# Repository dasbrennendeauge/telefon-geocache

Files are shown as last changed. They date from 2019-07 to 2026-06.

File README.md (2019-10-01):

## telefon-geocache

### Idee

Hörer abheben 
-> Ist die aktuelle Uhrzeit zwischen 8 und 22 Uhr? (RTC)
--> Nein? --> Displayanzeige "Dieses Gerät ist nur zwischen 8 und 22 Uhr verfügbar."

-> Arduino start -> GSM start
-> Displayanzeige "Hallo"
-> Sound abspielen "Hallo, willkommen zu meinem Cache. Du hast 5 Minuten Zeit und nur einen Versuch."
-> Display zeigt 5-Minuten-Zähler an

-> Displayanzeige & Sound: "Gib deine Handynummer ein und drücke die Rautetaste."

-> Zahleneingabe
-> Raute gedrückt?

-> Displayanzeige "Münze einwerfen"
-> Sound abspielen "Wirf eine Münze ein, damit das Spiel gestartet wird."

-> Münze eingeworfen? (Lichtschranke)
-> Displayanzeige & Sound: "Danke"

-> GSM bereit?
-> Verbindungsaufbau mit spezieller Rufnummer (z.B. 0211-1234-1337)
-> Klingeln?
-> Auflegen.

-> Displayanzeige & Sound: "Gib die letzten 4 Stellen des Anrufers ein."
-> Richtig?
-> Klappe unten öffnet (Relais)
-> Displayanzeige & Sound: "Trag dich ein, schließ die Klappe und häng auf."

### bisherige Umsetzung

(http://www.youtube.com/watch?v=i5rzEiwlTfw "")

### Benötigte Elektronik:
- Arduino Mega
- MP3-Player DFPlayerMini (2)
- Display	(2)
- Step Up Modul
- GSM-Modul	SIM800L (3)
- Keypad	(7)
- Lichtschranke (1)
- Relais SRD-05VDC-SL-C	(1)
- (Lautsprecher)

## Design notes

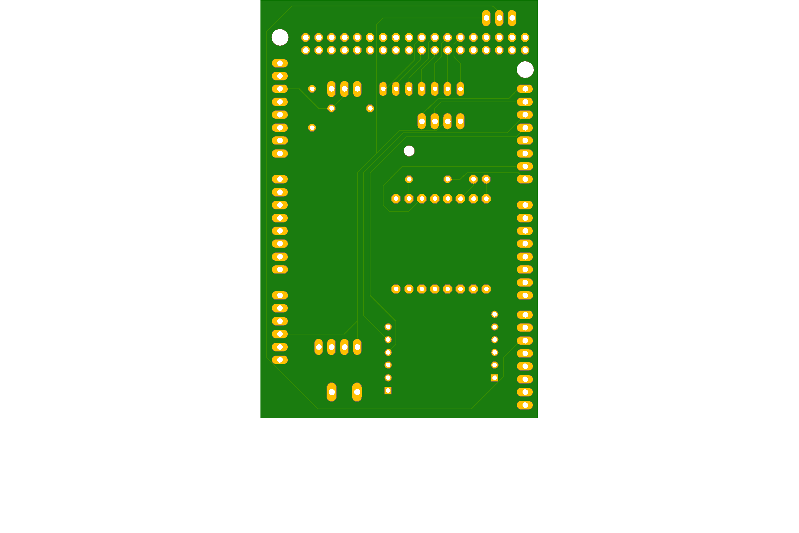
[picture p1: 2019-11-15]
pcb/cache/cache2-bottom.png

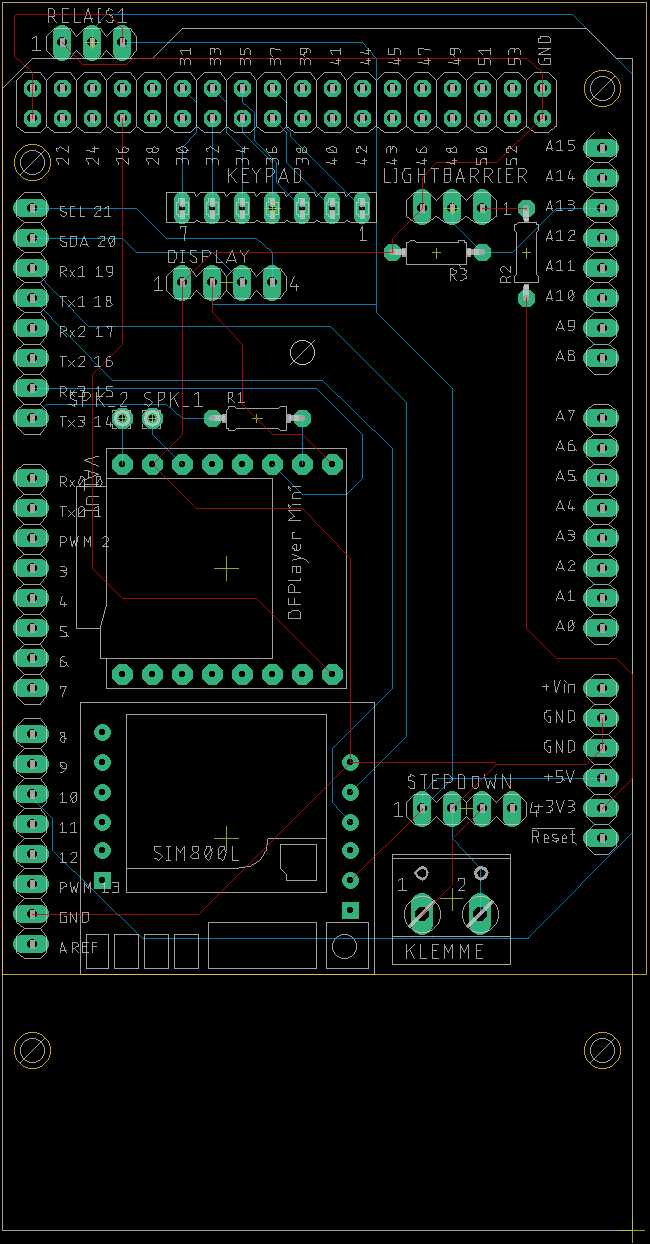
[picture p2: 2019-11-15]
pcb/cache/cache2-board.png

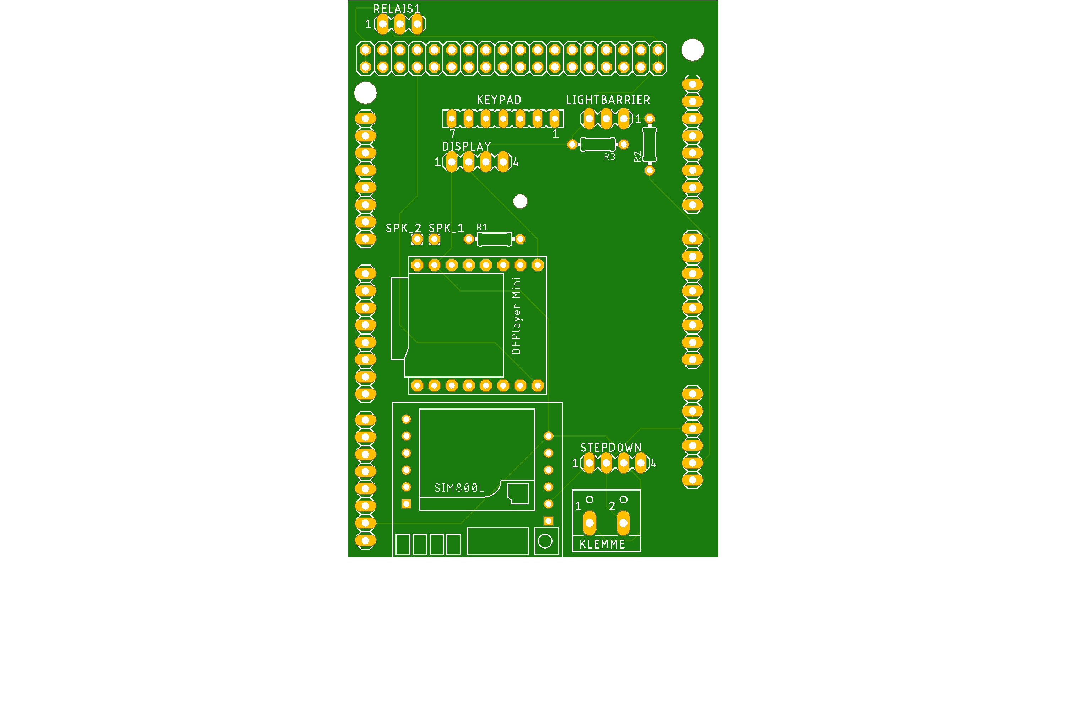
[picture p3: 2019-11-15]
pcb/cache/cache2-top.png

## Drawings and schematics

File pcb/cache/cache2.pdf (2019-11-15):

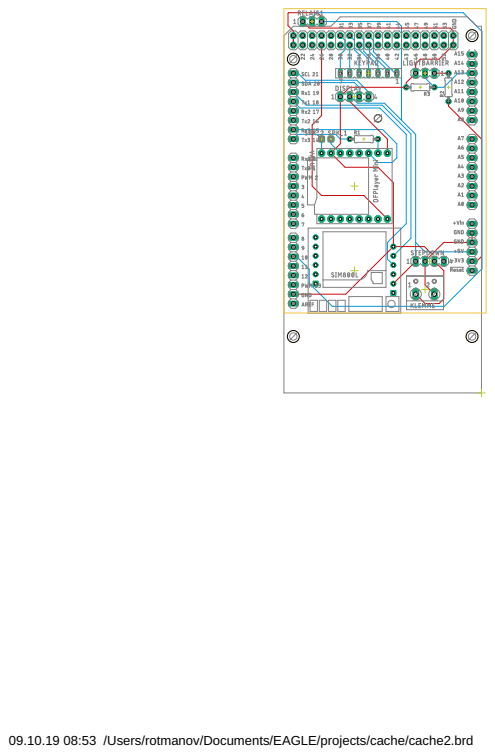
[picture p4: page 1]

09.10.19 08:53 /Users/rotmanov/Documents/EAGLE/projects/cache/cache2.brd

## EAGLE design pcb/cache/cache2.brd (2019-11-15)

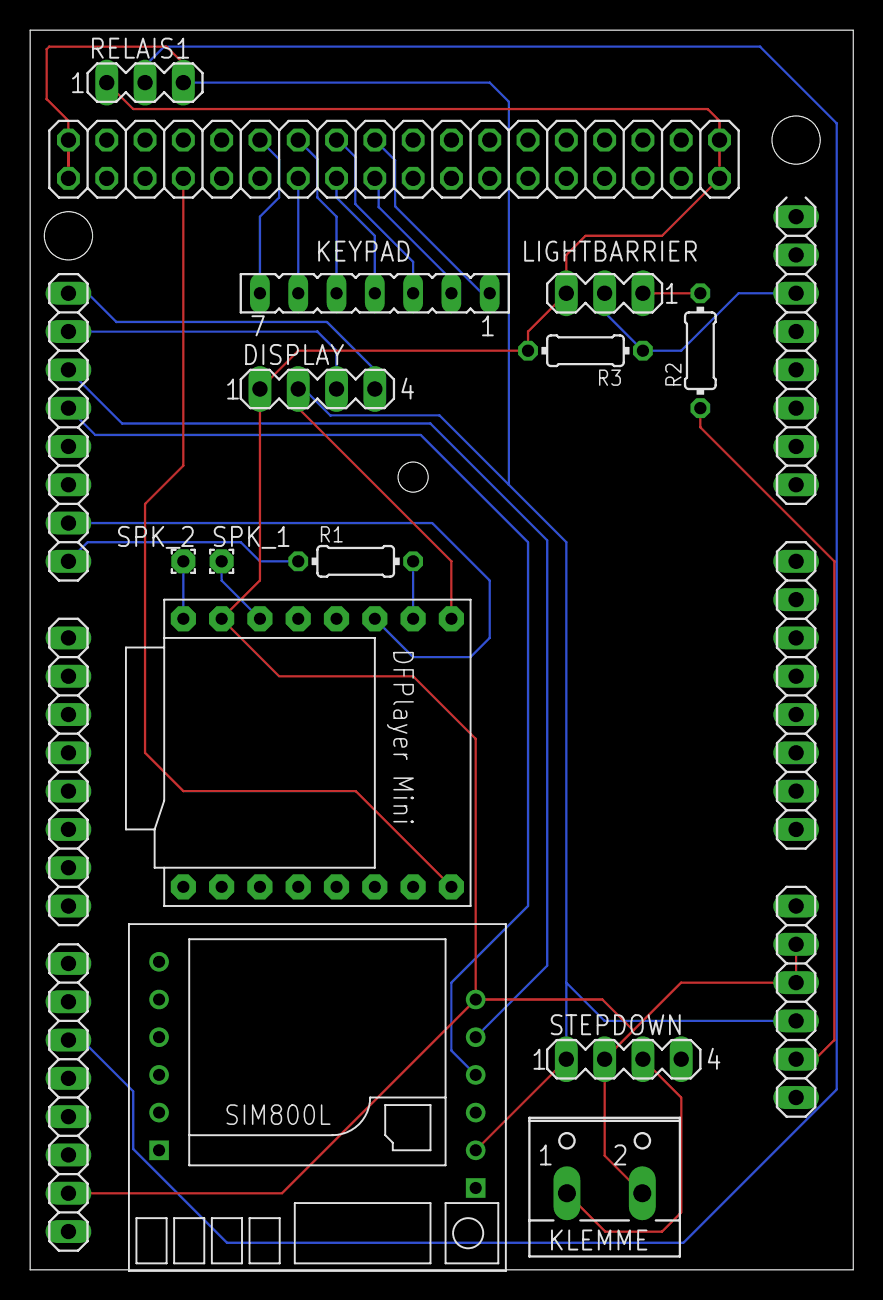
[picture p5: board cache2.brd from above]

Board: 2 copper layers, 54.6 x 82.2 mm, 14 parts (0 on the bottom side), 24 nets.

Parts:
DISPLAY: MA04-1
IC1: MEGA_ARDUINO
KEYPAD: FE07
KLEMME: W237-102
LIGHTBARRIER: MA03-1
R1, R2, R3: 0204/7
RELAIS1: MA03-1
SPK_1, SPK_2: 1,6/0,8
STEPDOWN: MA04-1
U$1: DFPLAYER
U$2: SIM800LMODULE

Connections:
3V3: LIGHTBARRIER.1, R2.2
+5V: DISPLAY.2, IC1.3, IC1.47, IC1.48, RELAIS1.3, STEPDOWN.1, U$1.VCC, U$2.VCC
GND: DISPLAY.1, IC1.4, IC1.5, IC1.45, IC1.81, IC1.82, KLEMME.2, LIGHTBARRIER.3, R3.2, RELAIS1.1, STEPDOWN.2, U$1.GND_1, U$2.GND
IN+: KLEMME.1, STEPDOWN.3
IN-B: IC1.20, LIGHTBARRIER.2, R3.1
unnamed: IC1.25, U$2.TX
unnamed: IC1.26, U$2.RX
unnamed: IC1.41, RELAIS1.2
unnamed: DISPLAY.3, IC1.24
unnamed: DISPLAY.4, IC1.23
unnamed: IC1.58, KEYPAD.7
unnamed: IC1.59, KEYPAD.6
unnamed: IC1.60, KEYPAD.5
unnamed: IC1.61, KEYPAD.4
unnamed: IC1.62, KEYPAD.3
unnamed: IC1.63, KEYPAD.2
unnamed: IC1.64, KEYPAD.1
unnamed: IC1.30, R1.1
unnamed: IC1.29, U$1.TX
unnamed: R1.2, U$1.RX
unnamed: IC1.2, R2.1
unnamed: SPK_2.1, U$1.SPK2
unnamed: SPK_1.1, U$1.SPK1
unnamed: IC1.53, U$1.BUSY

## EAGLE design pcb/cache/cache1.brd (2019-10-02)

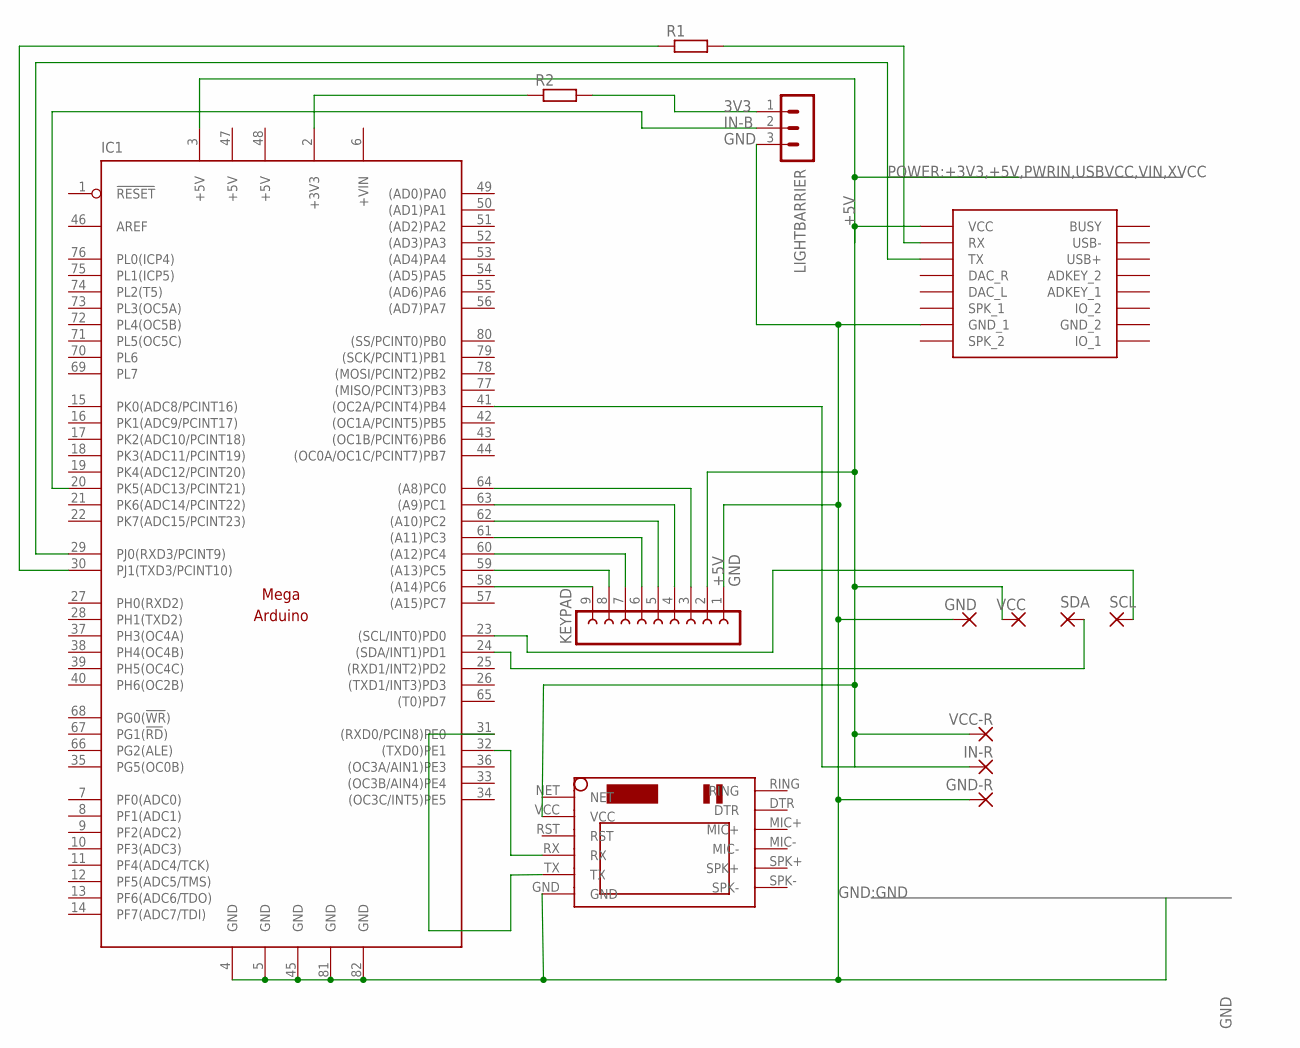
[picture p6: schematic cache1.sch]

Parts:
GND: 1,6/0,8
GND-R: 1,6/0,8
IC1: MEGAARDUINO_1; MEGA_ARDUINO
IN-R: 1,6/0,8
KEYPAD: FE09-1; FE09
LIGHTBARRIER: MA03-1
R1, R2: R-EU_0204/7; 0204/7
SCL: 1,6/0,8
SDA: 1,6/0,8
U$1: DFPLAYER
U$2: SIM800LMODULE
VCC: 1,6/0,8
VCC-R: 1,6/0,8

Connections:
3V3: LIGHTBARRIER.1, R2.2
+5V: IC1.3 (+5V), IC1.47 (+5V), IC1.48 (+5V), KEYPAD.2, U$1.VCC, U$2.VCC, VCC.1, VCC-R.1
+VIN: IC1.6 (+VIN)
GND: GND.1, GND-R.1, IC1.4 (GND), IC1.5 (GND), IC1.45 (GND), IC1.81 (GND), IC1.82 (GND), KEYPAD.1, LIGHTBARRIER.3, U$1.GND_1, U$2.GND
IN-B: IC1.20 (PK5(ADC13/PCINT21)), LIGHTBARRIER.2
unnamed: IC1.31 ((RXD0/PCIN8)PE0), U$2.TX
unnamed: IC1.32 ((TXD0)PE1), U$2.RX
unnamed: IC1.41 ((OC2A/PCINT4)PB4), IN-R.1
unnamed: IC1.24 ((SDA/INT1)PD1), SDA.1
unnamed: IC1.23 ((SCL/INT0)PD0), SCL.1
unnamed: IC1.58 ((A14)PC6), KEYPAD.9
unnamed: IC1.59 ((A13)PC5), KEYPAD.8
unnamed: IC1.60 ((A12)PC4), KEYPAD.7
unnamed: IC1.61 ((A11)PC3), KEYPAD.6
unnamed: IC1.62 ((A10)PC2), KEYPAD.5
unnamed: IC1.63 ((A9)PC1), KEYPAD.4
unnamed: IC1.64 ((A8)PC0), KEYPAD.3
unnamed: IC1.30 (PJ1(TXD3/PCINT10)), R1.1
unnamed: IC1.29 (PJ0(RXD3/PCINT9)), U$1.TX
unnamed: R1.2, U$1.RX
unnamed: IC1.2 (+3V3), R2.1

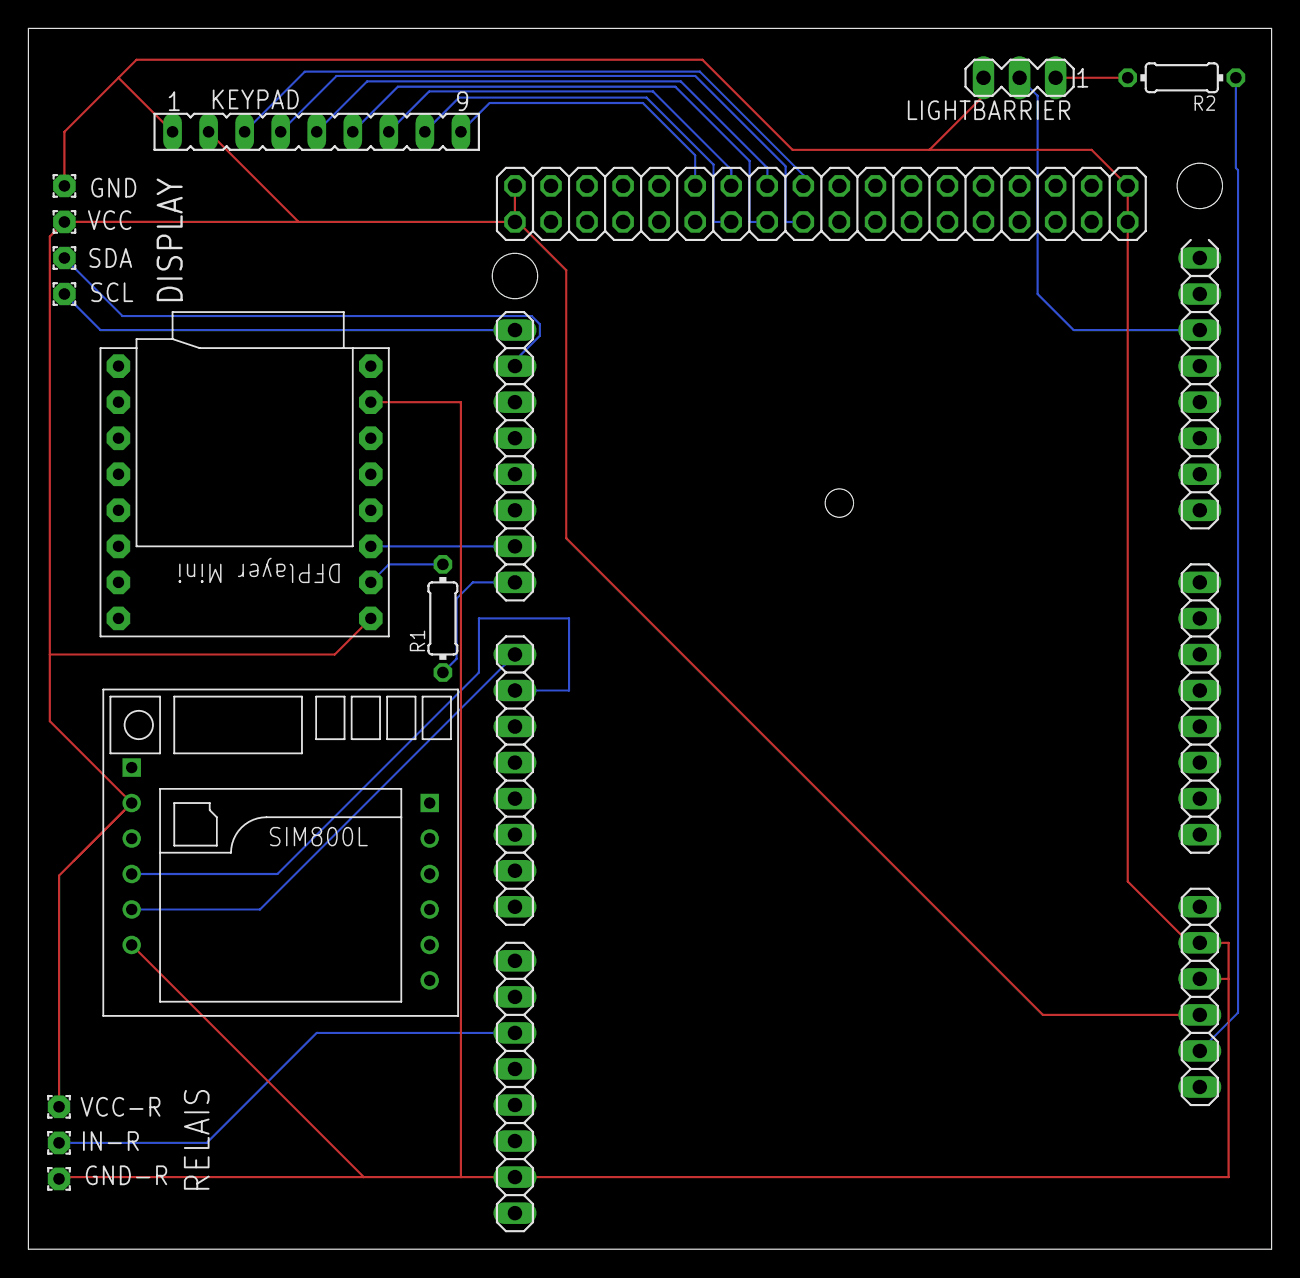
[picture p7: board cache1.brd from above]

Board: 2 copper layers, 87.6 x 86.0 mm, 14 parts (0 on the bottom side), 20 nets.

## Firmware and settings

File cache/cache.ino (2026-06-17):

#include <avr/sleep.h>
#include <LiquidCrystal_I2C.h>
#include <DFMiniMp3.h>
#include <SoftwareSerial.h>
#include <Keypad.h>

// GSM Calls: https://www.activexperts.com/serial-port-component/tutorials/gsmdial/

#define TIME_TO_LIVE 300
#define RELAIS_PIN 10
#define TINY_GSM_DEBUG Serial

const byte ROWS = 4; // Four rows
const byte COLS = 3; // Three columns
// Define the Keymap
char keys[ROWS][COLS] = {
  {'1', '2', '3'},
  {'4', '5', '6'},
  {'7', '8', '9'},
  {'#', '0', '*'}
};
// Connect keypad ROW0, ROW1, ROW2 and ROW3 to these Arduino pins.
byte rowPins[ROWS] = { 34, 35, 36, 37 };
// Connect keypad COL0, COL1 and COL2 to these Arduino pins.
byte colPins[COLS] = { 31, 32, 33 };
// Create the Keypad
Keypad kpd = Keypad( makeKeymap(keys), rowPins, colPins, ROWS, COLS );

const int analogInPin = A13;  // Data Muenzeinwurf

// set GSM PIN, if any
#define GSM_PIN "6348"

// DFPlayer Mini
SoftwareSerial mySoftwareSerial(2, 3); // RX, TX
// implement a notification class,
// its member methods will get called
//
class Mp3Notify {
  public:
    static void OnError(uint16_t errorCode) {
      // see DfMp3_Error for code meaning
      Serial.println();
      Serial.print("Com Error ");
      Serial.println(errorCode);
    }
    static void OnPlayFinished(uint16_t track) {
      Serial.print("Track beendet ");
      Serial.println(track);
      delay(100);
      // TODO: nächsten Schritt aufrufen
    }
    static void OnCardOnline(uint16_t code) {
      Serial.println(F("SD Karte online "));
    }
    static void OnCardInserted(uint16_t code) {
      Serial.println(F("SD Karte bereit "));
    }
    static void OnCardRemoved(uint16_t code) {
      Serial.println(F("SD Karte entfernt "));
    }
    static void OnUsbOnline(uint16_t code) {
      Serial.println(F("USB online "));
    }
    static void OnUsbInserted(uint16_t code) {
      Serial.println(F("USB bereit "));
    }
    static void OnUsbRemoved(uint16_t code) {
      Serial.println(F("USB entfernt "));
    }
};
static DFMiniMp3<HardwareSerial, Mp3Notify> mp3(Serial3);

LiquidCrystal_I2C lcd(0x27, 20, 4); //Hier wird das Display benannt. In unserem //Fall „lcd“. Die I²C Adresse (Erläuterung und I²C Adressen Scanner in folgender Anleitung: Link zur Anleitung „2 I²C Displays gleichzeitig“) 0x27 wird auch angegeben.

// Select your modem:
#define TINY_GSM_MODEM_SIM800

// Increase RX buffer to capture the entire response
// Chips without internal buffering (A6/A7, ESP8266, M590)
// need enough space in the buffer for the entire response
// else data will be lost (and the http library will fail).
#define TINY_GSM_RX_BUFFER 512

// Set serial for AT commands (to the module)
// Use Hardware Serial on Mega
// RX118 & TX119
#define SerialAT Serial1

// Your GPRS credentials
// Leave empty, if missing user or pass
const char apn[]  = "sipgate";
const char gprsUser[] = "sipgate";
const char gprsPass[] = "sipgate";

// Server details
const char server[] = "dev.rotmanov.de";
String url = String("/?number=");
const int port = 9992;

#include <TinyGsmClient.h>
#include <ArduinoHttpClient.h>

TinyGsm modem(SerialAT);
TinyGsmClient client(modem);
HttpClient http(client, server, port);

unsigned long startMillis;
unsigned long stepStartMillis;
int step = 0;
bool refreshDisplay = false;
bool outOfOrder = false;

String phoneNumber = String("");

String expected = String("4711"); // TODO: ersetze mit angerufener Nummer
String pin = String("");

void setup() {
  Serial.begin(115200); // Es gibt ein paar Debug Ausgaben über die serielle Schnittstelle
  Serial.println("Arduino start");

  pinMode(RELAIS_PIN, OUTPUT);
  digitalWrite(RELAIS_PIN, HIGH); //An dieser Stelle würde das Relais einsschalten

  // DFPlayer Mini initialisieren
  mp3.begin();
  mp3.setVolume(15);

  // -> Arduino start -> GSM start
  lcd.begin();
  lcd.backlight();//Beleuchtung des Displays einschalten
  startMillis = millis();
  refreshDisplay = true;
}

// -> Displayanzeige "Hallo, willkommen zu meinem Cache. Du hast 5 Minuten Zeit und nur einen Versuch."
// -> Sound abspielen "Hallo, willkommen zu meinem Cache. Du hast 5 Minuten Zeit und nur einen Versuch."
// -> Display zeigt 5-Minuten-Zähler an

void loop() {
  mp3.loop();
  if (step == 0) {
    step0();
  } else if (step == 1) {
    step1();
  } else if (step == 2) {
    step2();
  } else if (step == 3) {
    step3();
  } else if (step == 4) {
    step4();
  } else if (step == 5) {
    step5();
  } else if (step == 6) {
    step6();
  } else if (step == 7) {
    step7();
  }
  decreaseTimer();
}

void step0() {
  if (refreshDisplay == true) {
    showText(
      "H\xEFrer ans Ohr!      ",
      "                    ",
      "Dr""\xF5""cke dann Taste 5 ");
    refreshDisplay = false;

    // Set GSM module baud rate
    SerialAT.begin(19200);
    Serial.println("GSM start");

    // Restart takes quite some time
    // To skip it, call init() instead of restart()
    Serial.println("Initializing modem...");
    // modem.restart();
    modem.init();

    String modemInfo = modem.getModemInfo();
    Serial.print("Modem: ");
    Serial.println(modemInfo);

    if ( GSM_PIN && modem.getSimStatus() != 3 ) {
      modem.simUnlock(GSM_PIN);
    }
  }

  /*
  unsigned long currentMillis = millis();
  int secondsElapsed = (currentMillis - startMillis) / 1000;
  if (secondsElapsed > 2) {
  */
  char key = kpd.getKey();
  if (key) {
    step = 1;
    mp3.playMp3FolderTrack(1);
    stepStartMillis = millis();
    refreshDisplay = true;
  }
}

void step1() {
  if (refreshDisplay == true) {
    showText(
      "Willkommen!         ",
      "Deine Zeit l\xE1uft... ",
      "                    ");
    refreshDisplay = false;

  unsigned long startMillis = millis();
    Serial.println("Waiting for network...");

    modem.waitForNetwork();
    if (modem.isNetworkConnected()) {
      unsigned long currentMillis = millis();
      int secondsElapsed = (currentMillis - startMillis) / 1000;
      Serial.print("Network connected");
      Serial.println(secondsElapsed);
    }

    delay(500);
    
    String gsmTime = modem.getGSMDateTime(DATE_TIME);
    Serial.print("GSM Time:");
    Serial.println(gsmTime);
    String hour = gsmTime.substring(0, 2);
    Serial.println(hour);
    int hourI = hour.toInt();
    if(hourI > 21) {
      outOfOrder = true;
    }
    if(hourI < 8) {
      outOfOrder = true;
    }
    // String gsmDate = modem.getGSMDateTime(DATE_DATE);
    // Serial.print("GSM Date:");
    // Serial.println(gsmDate);
  }

  unsigned long currentMillis = millis();
  int secondsElapsed = (currentMillis - stepStartMillis) / 1000;
  if (secondsElapsed > 6) {
    if(outOfOrder) {
      stepStartMillis = millis();
      step = 7;
    } else {
      step = 2;      
      mp3.playMp3FolderTrack(2);
    }
    refreshDisplay = true;
  }
}

void step2() {
  if (refreshDisplay == true) {
    lcd.clear();
    showText(
      "Deine Handynummer:  ",
      phoneNumber.c_str(),
      "Ende mit Leertaste  ");
    refreshDisplay = false;
  }

  char key = kpd.getKey();
  if (key) {
    if (key == '#') {
      step = 3;
      url.concat(phoneNumber);
      mp3.playMp3FolderTrack(3);
      refreshDisplay = true;
      return;
    }
    phoneNumber.concat(key);
    refreshDisplay = true;
  }
}

void step3() {
  if (refreshDisplay == true) {
    showText(
      "M\xF5nze einwerfen     ",
      "                    ",
      "(Keine R""\xF5""ckgabe)    ");

    refreshDisplay = false;
  }

  // read the analog in value:
  int sensorValue = analogRead(analogInPin);

  if (sensorValue != 0) {
    step = 4;
    mp3.playMp3FolderTrack(4);
    stepStartMillis = millis();
    refreshDisplay = true;
    Serial.println("Pling!");
  }
}

void step4() {
  if (refreshDisplay == true) {
    showText(
      "Danke.              ",
      "Ich rufe dich an.   ",
      "NICHT ABHEBEN!      ");

    Serial.print("Waiting for network...");
    if (!modem.waitForNetwork()) {
      Serial.println(" fail");
      delay(10000);
      return;
    }
    Serial.println(" OK");

    if (modem.isNetworkConnected()) {
      Serial.println("Network connected");
    }

    Serial.print(F("Connecting to "));
    Serial.print(apn);
    if (!modem.gprsConnect(apn, gprsUser, gprsPass)) {
      Serial.println(" fail");
      delay(10000);
      return;
    }
    Serial.println(" OK");

    Serial.print(F("Performing HTTP GET request... "));
    Serial.print(url);
    int err = http.get(url);
    if (err != 0) {
      Serial.println(F("failed to connect"));
      delay(10000);
      return;
    }

    int status = http.responseStatusCode();
    Serial.print(F("Response status code: "));
    Serial.println(status);
    if (!status) {
      delay(10000);
      return;
    }

    String body = http.responseBody();
    Serial.println(F("Response:"));
    Serial.println(body);

    Serial.print(F("Body length is: "));
    Serial.println(body.length());

    expected = body;

    // Shutdown
    http.stop();
    Serial.println(F("Server disconnected"));

    modem.gprsDisconnect();
    Serial.println(F("GPRS disconnected"));

    step = 5;
    mp3.playMp3FolderTrack(5);
    refreshDisplay = true;
  }
}

void step5() {
  if (refreshDisplay == true) {
    lcd.clear();
    showText(
      "Wer rief dich an?   ",
      "Gib letzte 4 Zahlen:",
      pin.c_str());
    refreshDisplay = false;
  }

  char key = kpd.getKey();
  if (key) {
    pin.concat(key);
    if (pin.length() == 4) {
      step = 6;
      refreshDisplay = true;
      return;
    }
    refreshDisplay = true;
  }
}

void step6() {
  if (refreshDisplay == true) {
    lcd.clear();
    if (pin == expected) {

      digitalWrite(RELAIS_PIN, LOW); //An dieser Stelle würde das Relais einsschalten
      delay(500);//...eine Sekunde warten
      digitalWrite(RELAIS_PIN, HIGH); //Und wieder ausschalten

      mp3.playMp3FolderTrack(6);
      showText(
        "Geschafft.          ",
        "Trag dich ein, dann ",
        "Klappe zu.          ");
    } else {
      mp3.playMp3FolderTrack(8);
      showText(
        "PIN nicht korrekt :(",
        "Auflegen &          ",
        "neu versuchen       ");
    }
    refreshDisplay = false;
  }
}

// ausserhalb oeffnungszeiten
void step7() {
  if (refreshDisplay == true) {
    lcd.clear();
      mp3.playMp3FolderTrack(7);
      showText(
        "Cache-Zeit von      ",
        "8 Uhr bis 22 Uhr    ",
        "Sorry. :'-(         ");
    refreshDisplay = false;
  }

  unsigned long currentMillis = millis();
  int secondsElapsed = (currentMillis - stepStartMillis) / 1000;
  if (secondsElapsed > 6) {
    enterSleep();
  }
  
}

void showText(char *line1, char *line2, char *line3) {
  lcd.setCursor(0, 0); //Text soll beim ersten Zeichen in der ersten Reihe beginnen..
  lcd.print(line1); //In der ersten Zeile soll der Text „Test Zeile 1“ angezeigt werden
  lcd.setCursor(0, 1); //Genauso geht es bei den weiteren drei Zeilen weiter
  lcd.print(line2);
  lcd.setCursor(0, 2);
  lcd.print(line3);
  Serial.println(line1);
  Serial.println(line2);
  Serial.println(line3);
}

void decreaseTimer() {
  unsigned long currentMillis = millis();
  int secondsRemaining = TIME_TO_LIVE - ((currentMillis - startMillis) / 1000);
  if (secondsRemaining <= 0) {
    enterSleep();
  }
  char line[20] = "";
  sprintf(line, "%3d Sekunden   ", secondsRemaining);
  lcd.setCursor(0, 3);
  lcd.print(line);
}

void enterSleep() {
  lcd.clear();
  lcd.noBacklight();
  set_sleep_mode(SLEEP_MODE_PWR_DOWN);
  sleep_enable();
  sleep_mode();
}

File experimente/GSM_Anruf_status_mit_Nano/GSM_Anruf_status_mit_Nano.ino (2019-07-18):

/**************************************************************
 *
 * TinyGSM Getting Started guide:
 *   https://tiny.cc/tinygsm-readme
 *
 * NOTE:
 * Some of the functions may be unavailable for your modem.
 * Just comment them out.
 *
 **************************************************************/

// Select your modem:
#define TINY_GSM_MODEM_SIM800

// Define the serial console for debug prints, if needed
#define TINY_GSM_DEBUG SerialMon

// Set serial for debug console (to the Serial Monitor, default speed 115200)
#define SerialMon Serial

// or Software Serial on Uno, Nano
#include <SoftwareSerial.h>
SoftwareSerial SerialAT(8,7); // RX, TX

/*
 * Test enabled
 */
#define TINY_GSM_TEST_GPRS true
#define TINY_GSM_TEST_CALL true
#define TINY_GSM_POWERDOWN true

// set GSM PIN, if any
#define GSM_PIN ""

// Set phone numbers, if you want to test SMS and Calls
#define CALL_TARGET "+49XXXXXXXXXXXX"

// Your GPRS credentials
// Leave empty, if missing user or pass
const char apn[]  = "sipgate";
const char gprsUser[] = "sipgate";
const char gprsPass[] = "sipgate";

#include <TinyGsmClient.h>

TinyGsm modem(SerialAT);

void setup() {
  // Set console baud rate
  SerialMon.begin(115200);
  delay(10);

  DBG("Wait...");

  SerialAT.begin(19200);
  delay(3000);
}

void loop() {

  // Restart takes quite some time
  // To skip it, call init() instead of restart()
  DBG("Initializing modem...");
  // if (!modem.restart()) {
  if (!modem.init()) {
    DBG("Failed to restart modem, delaying 10s and retrying");
    delay(3000);
    return;
  }

  String name = modem.getModemName();
  DBG("Modem Name:", name);

  String modemInfo = modem.getModemInfo();
  DBG("Modem Info:", modemInfo);

#if TINY_GSM_TEST_GPRS
  // Unlock your SIM card with a PIN if needed
  if ( GSM_PIN && modem.getSimStatus() != 3 ) {
    modem.simUnlock(GSM_PIN);
  }
#endif

#if TINY_GSM_TEST_WIFI
  DBG("Setting SSID/password...");
  if (!modem.networkConnect(wifiSSID, wifiPass)) {
    DBG(" fail");
    delay(10000);
    return;
  }
  SerialMon.println(" OK");
#endif

#if TINY_GSM_TEST_GPRS && defined TINY_GSM_MODEM_XBEE
  // The XBee must run the gprsConnect function BEFORE waiting for network!
  modem.gprsConnect(apn, gprsUser, gprsPass);
#endif

  DBG("Waiting for network...");
  if (!modem.waitForNetwork()) {
    delay(10000);
    return;
  }

  if (modem.isNetworkConnected()) {
    DBG("Network connected");
  }

#if TINY_GSM_TEST_GPRS
  DBG("Connecting to", apn);
  if (!modem.gprsConnect(apn, gprsUser, gprsPass)) {
    delay(10000);
    return;
  }

  bool res = modem.isGprsConnected();
  DBG("GPRS status:", res ? "connected" : "not connected");

  String ccid = modem.getSimCCID();
  DBG("CCID:", ccid);

  String imei = modem.getIMEI();
  DBG("IMEI:", imei);

  String cop = modem.getOperator();
  DBG("Operator:", cop);

  IPAddress local = modem.localIP();
  DBG("Local IP:", local);

  int csq = modem.getSignalQuality();
  DBG("Signal quality:", csq);

  // This is only supported on SIMxxx series
  String gsmLoc = modem.getGsmLocation();
  DBG("GSM location:", gsmLoc);

  // This is only supported on SIMxxx series
  String gsmTime = modem.getGSMDateTime(DATE_TIME);
  DBG("GSM Time:", gsmTime);
  String gsmDate = modem.getGSMDateTime(DATE_DATE);
  DBG("GSM Date:", gsmDate);
#endif

#if TINY_GSM_TEST_CALL && defined(CALL_TARGET)
  DBG("Calling:", CALL_TARGET);

  res = modem.callNumber(CALL_TARGET);
  DBG("Call:", res ? "OK" : "fail");

  int i = 0;
  while ((getCallStatus() == 4) || i == 10) {
    DBG("Rufaufbau");
    i++;
    delay(1000L);
  }

/*
  values of return:
 0 Ready (MT allows commands from TA/TE)
 2 Unknown (MT is not guaranteed to respond to tructions)
 3 Ringing (MT is ready for commands from TA/TE, but the ringer is active)
 4 Call in progress
*/
  
  if (res) {
    delay(10000L);

    res = modem.callHangup();
    DBG("Hang up:", res ? "OK" : "fail");
  }
#endif

#if TINY_GSM_TEST_BATTERY
  uint8_t chargeState = -99;
  int8_t percent = -99;
  uint16_t milliVolts = -9999;
  modem.getBattStats(chargeState, percent, milliVolts)
  DBG("Battery charge state:", chargeState);
  DBG("Battery charge 'percent':", percent);
  DBG("Battery voltage:", milliVolts / 1000.0F);

  float temp = modem.getTemperature();
  DBG("Chip temperature:", temp);
#endif

#if TINY_GSM_TEST_GPRS
  modem.gprsDisconnect();
  if (!modem.isGprsConnected()) {
    DBG("GPRS disconnected");
  } else {
    DBG("GPRS disconnect: Failed.");
  }
#endif

#if TINY_GSM_POWERDOWN
  // Try to power-off (modem may decide to restart automatically)
  // To turn off modem completely, please use Reset/Enable pins
  modem.poweroff();
  DBG("Poweroff.");
#endif

  // Do nothing forevermore
  while (true) {
    modem.maintain();
  }
}

int getCallStatus() {  
  modem.sendAT(GF("+CPAS"));
  if (modem.waitResponse(2000L, GF(GSM_NL "+CPAS: ")) != 1) {
        DBG("Nix bekommen");
        return -1;
  }
  int callStatus = SerialAT.readStringUntil('\n').toInt();
  modem.waitResponse();
  DBG(callStatus);  
  return callStatus;
}

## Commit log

2019-03-05 schritt 1: display anzeige und counter
2019-03-06 Formatierung und Wort "Sekunden" beim Countdown hinzugefügt
2019-04-30 Muenzeinwurf funktioniert, PIN-Eingabe, Ergebnisanzeige
2019-07-31 added php script to start and hang up call - returns PIN code
2019-08-08 funktionierende Beispiele mit Nano und GSM
2019-10-02 PCB hinzugefuegt
    [cache1.brd, cache1.sch]
2019-11-15 updated pcb
    [cache2.brd, cache2.sch, cache3.brd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]

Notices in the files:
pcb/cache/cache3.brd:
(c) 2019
